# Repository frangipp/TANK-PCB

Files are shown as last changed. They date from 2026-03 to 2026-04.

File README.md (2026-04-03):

Dans le cadre d’un projet étudiant en binôme à l’ESEO Angers.

Développement d’un "TANK" : un petit robot à entraînement différentiel. Il sera commandé par Bluetooth via une application Android.
Pour l’utilisateur, l’objectif sera d’entrer en collision avec le TANK adverse. Chaque collision rapporte des points.

Détails techniques :

* Microcontrôleur STM32G431
* Module Bluetooth HC-05
* Négociation USB Power Delivery (STUSB4531)
* Chargeur et BMS pour batterie Li-ion (power management : BQ24800, équilibrage des cellules : BQ76905)
* Driver moteur LMD18200. Moteurs jusqu’à 55 V (théorique) et 3 A. On utilise ici des Maxon en 12 V.

À titre personnel, ce projet me permet surtout de tester la norme USB Power Delivery ainsi que la charge d’une batterie.

### Restrictions on Automated Processing and AI Usage

The author explicitly prohibits any text and data mining (TDM), scraping, indexing, or use of this project for training, evaluating, or operating artificial intelligence systems, unless prior written permission is obtained.

All rights are reserved in this regard, including under applicable EU directives on text and data mining.

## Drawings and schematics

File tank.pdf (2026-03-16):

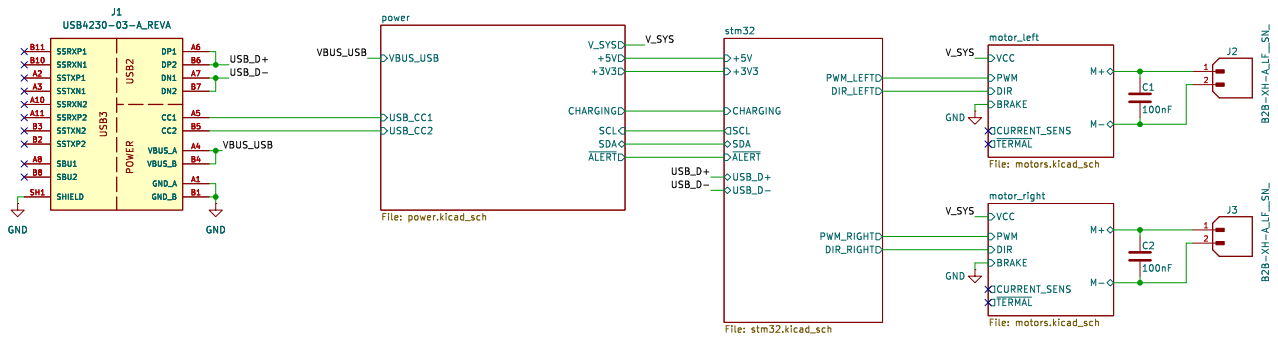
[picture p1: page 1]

motor_right File: motors.kicad_sch SCL SDA

Id: 1/6 Title: File: tank.kicad_sch Sheet: /

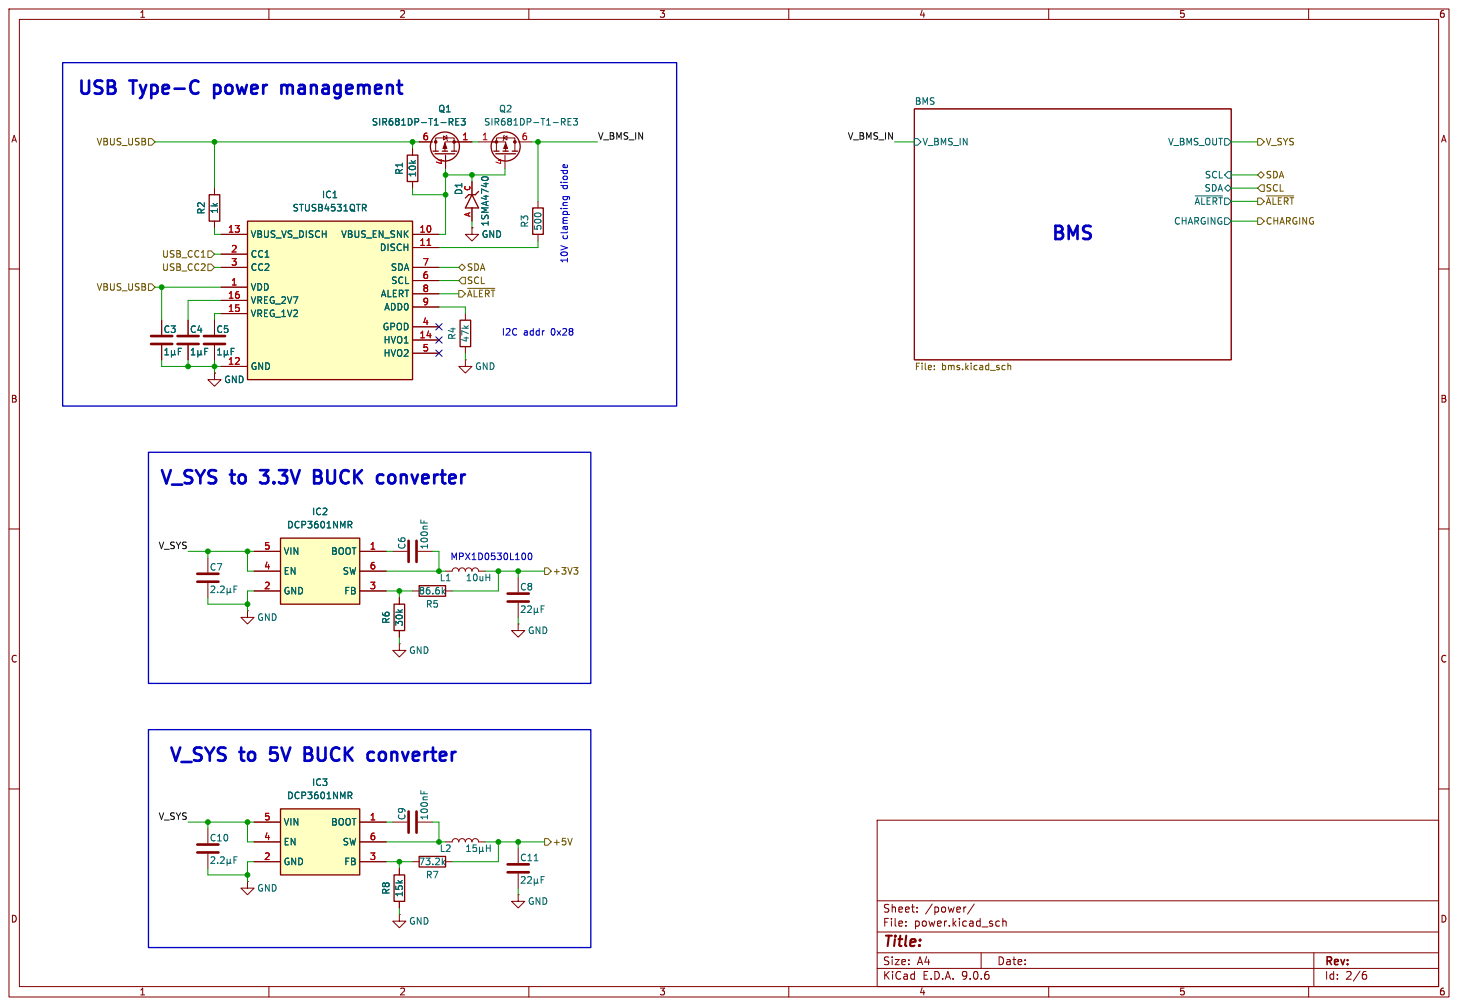
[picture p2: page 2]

Id: 2/6 Title: File: power.kicad_sch Sheet: /power/

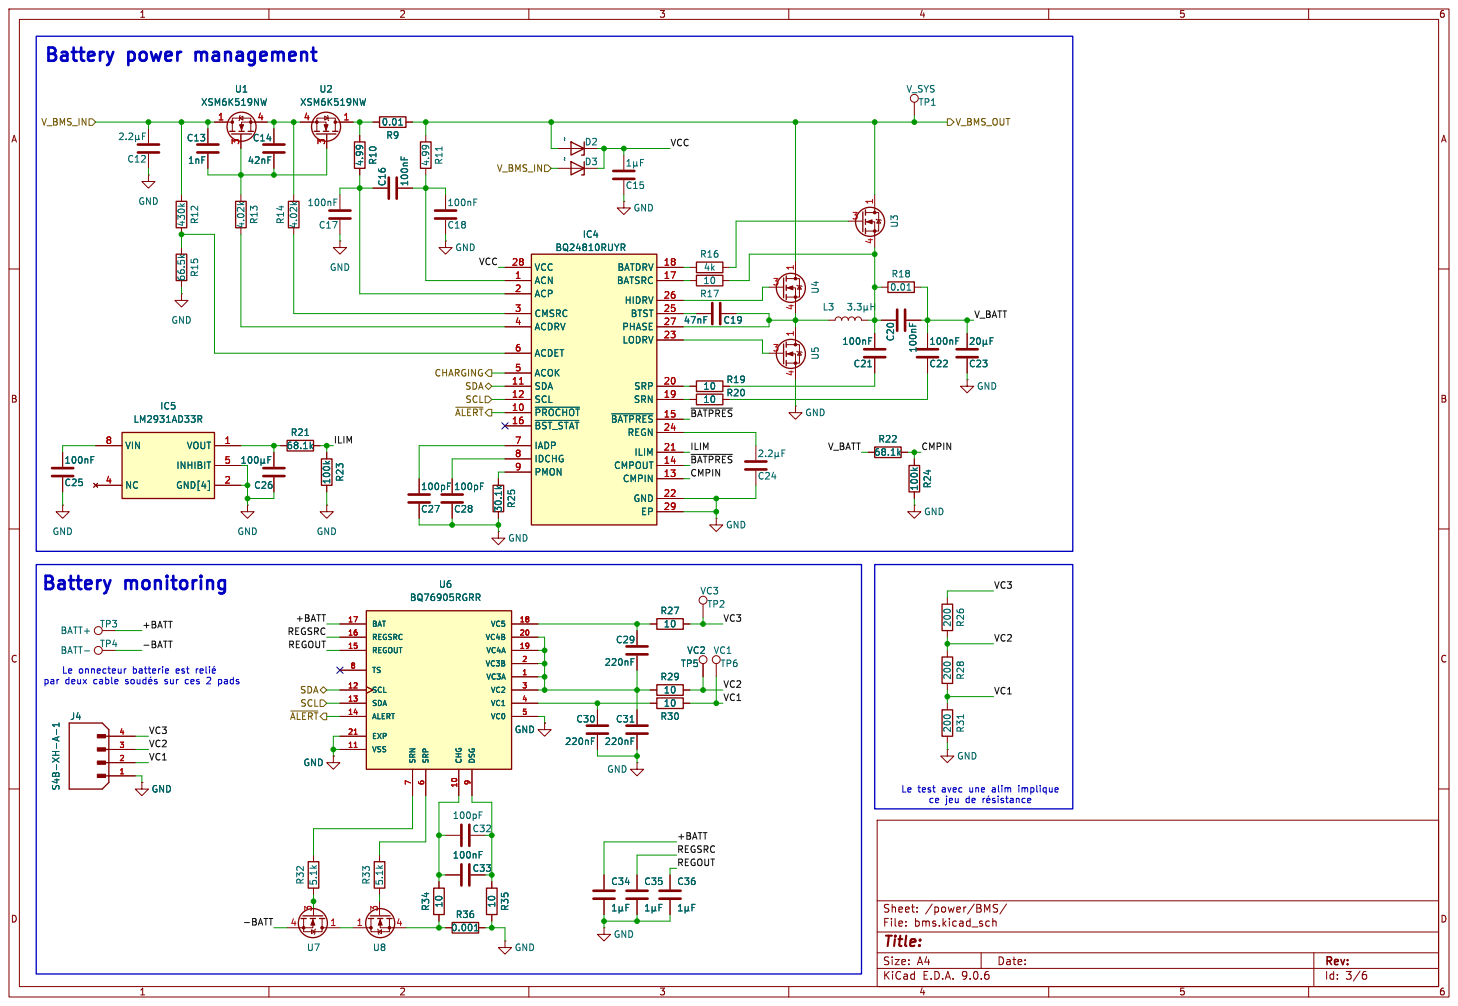
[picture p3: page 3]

Id: 3/6 Title: File: bms.kicad_sch Sheet: /power/BMS/ GND

ce jeu de þÿrésistance

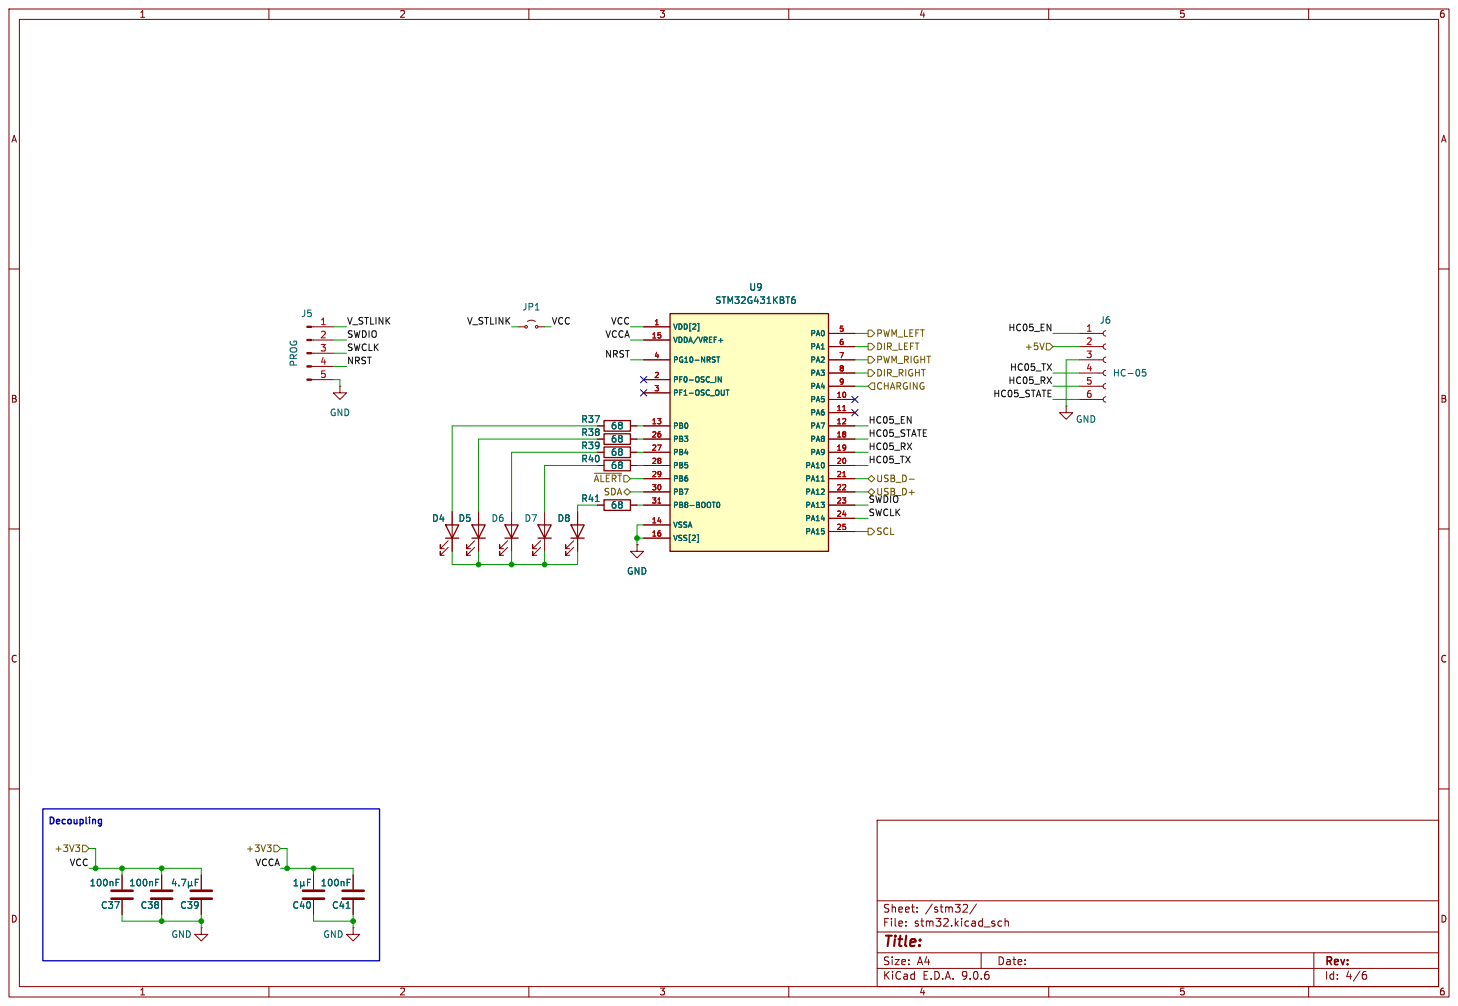
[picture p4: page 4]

þÿ1µFGND
Id: 4/6 Title: File: stm32.kicad_sch Sheet: /stm32/ C40

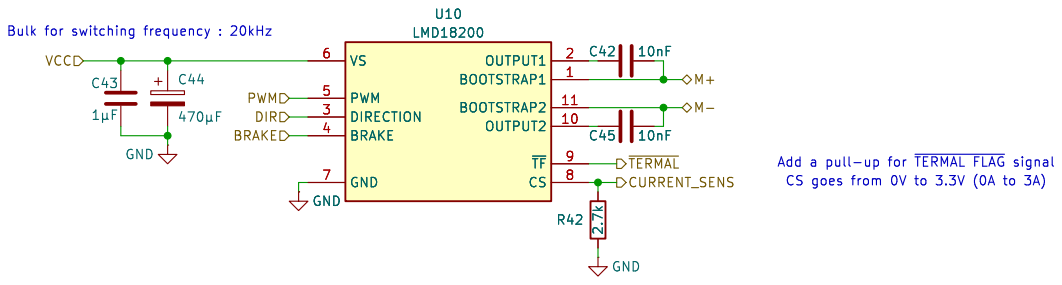
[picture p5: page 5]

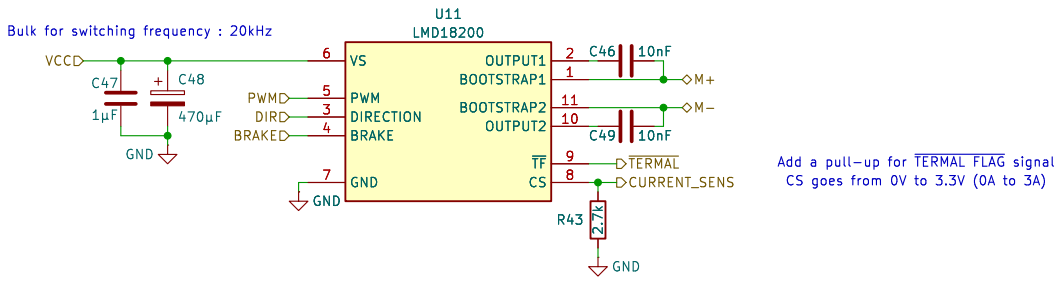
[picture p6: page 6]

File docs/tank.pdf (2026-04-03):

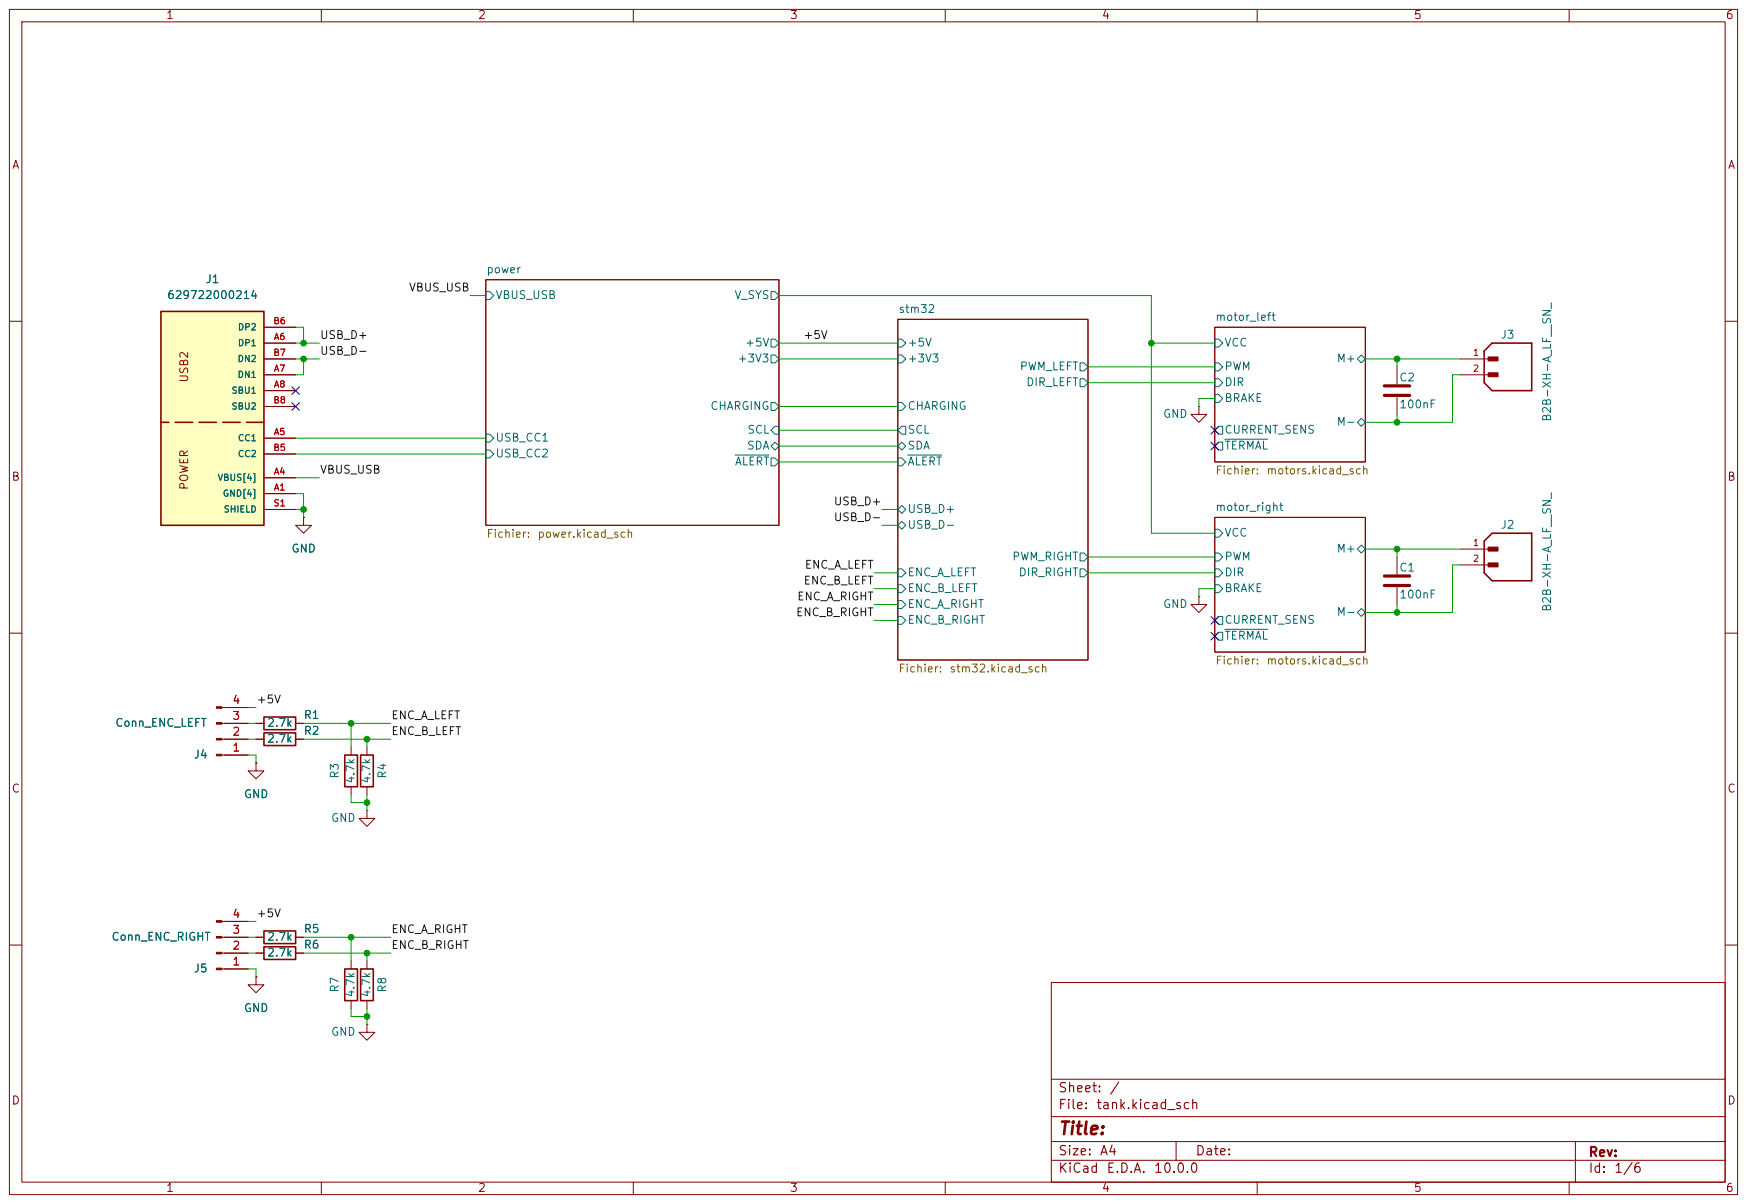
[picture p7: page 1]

TERMAL motor_left Fichier: motors.kicad_sch GND

Size: A4 | Rev:
KiCad E.D.A. 10.0.0 | Id: 1/6

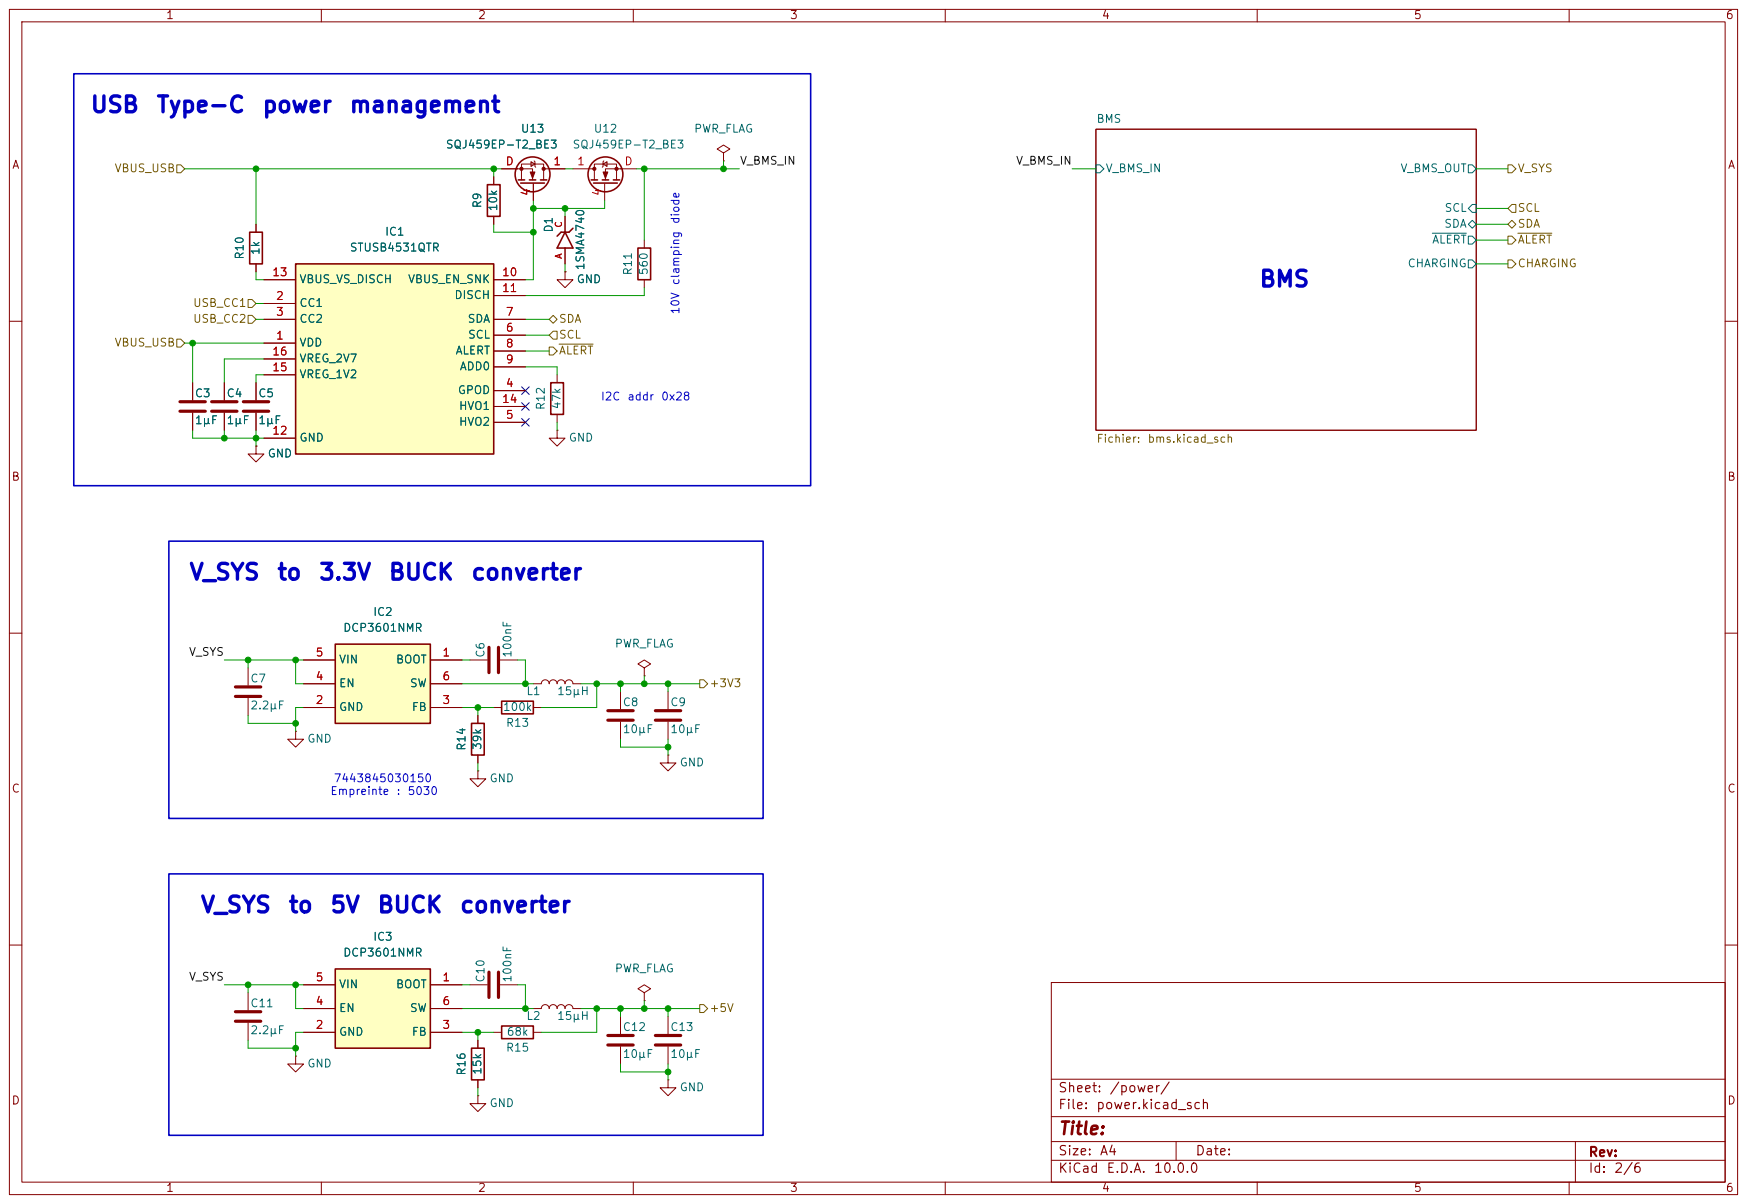
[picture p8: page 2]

USB Type-C power management

Empreinte : 5030 V_SYS to 5V BUCK converter

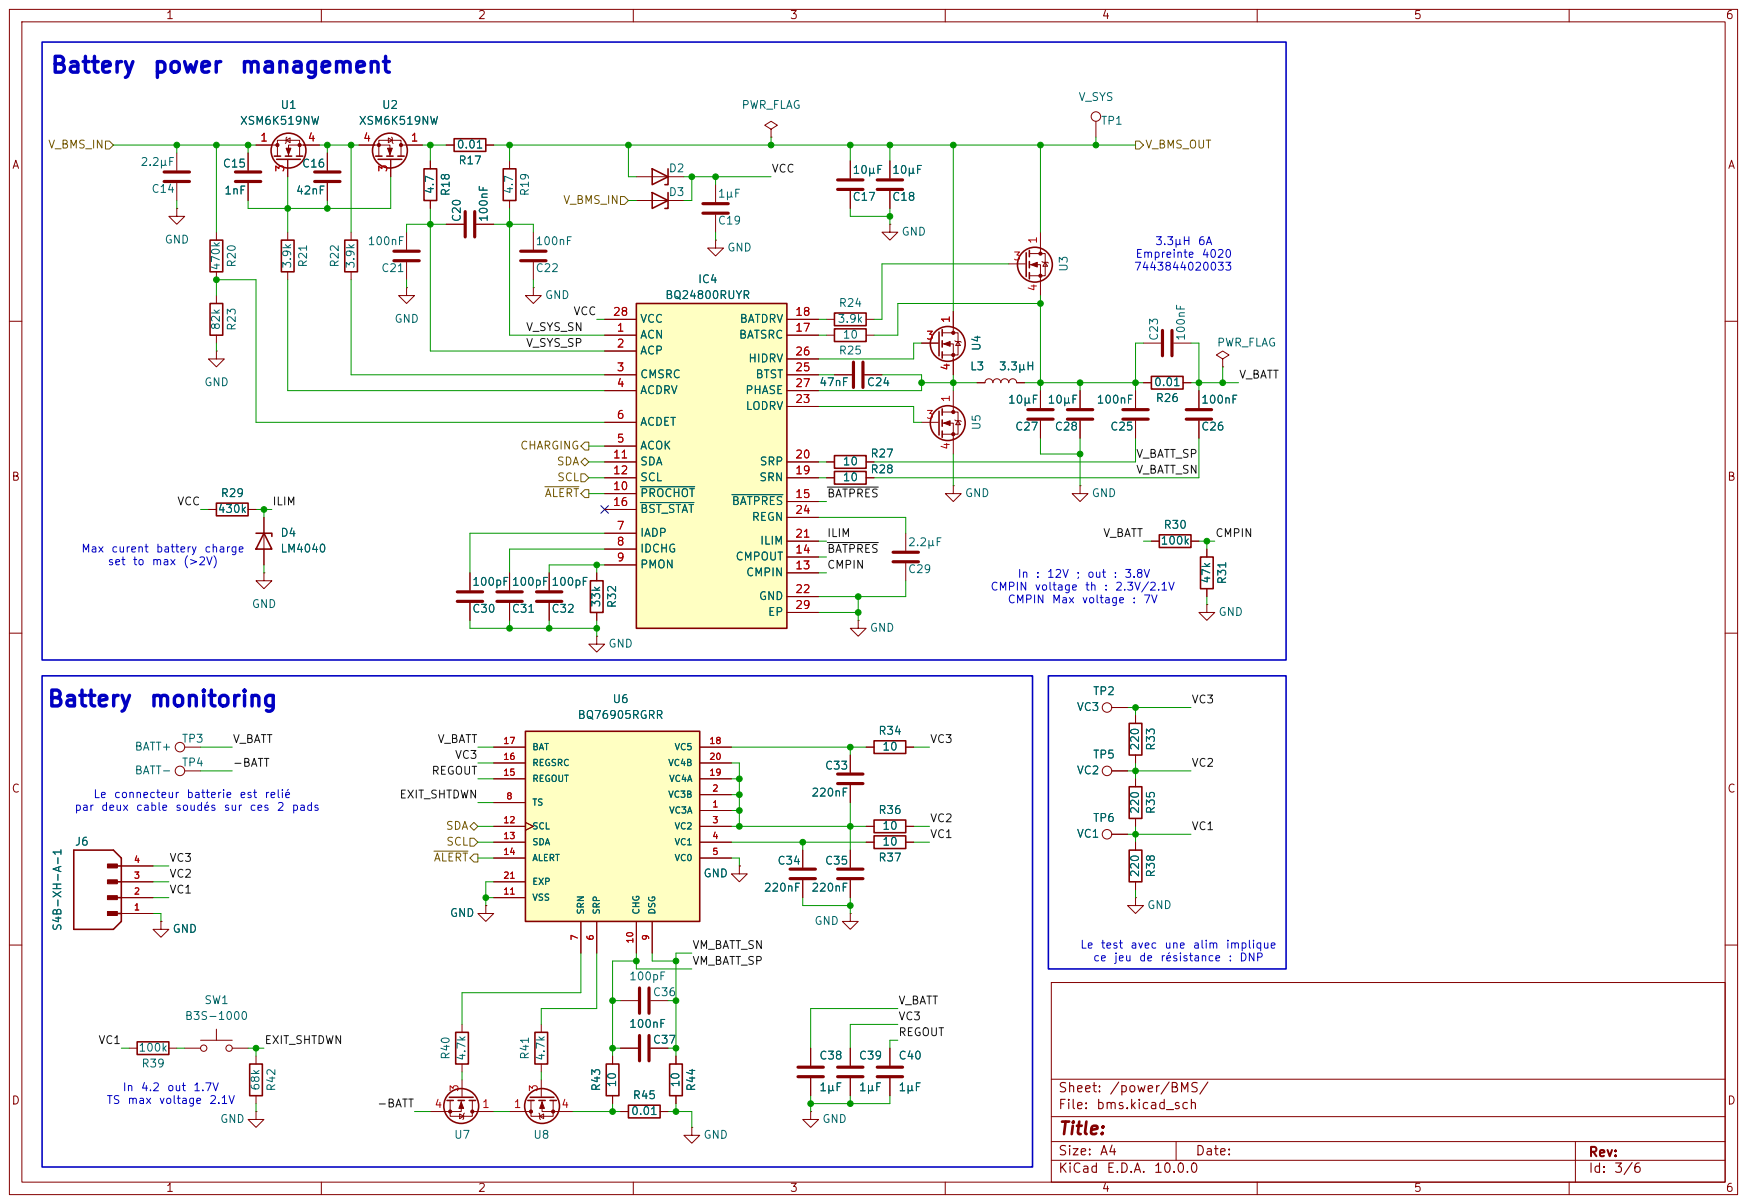
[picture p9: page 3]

ILIM Battery power management

Max curent battery charge

In : 12V ; out : 3.8V CMPIN voltage th : 2.3V/2.1V

Le connecteur batterie est relié par deux cable soudés sur ces 2 pads

Le test avec une alim implique
ce jeu de résistance : DNP

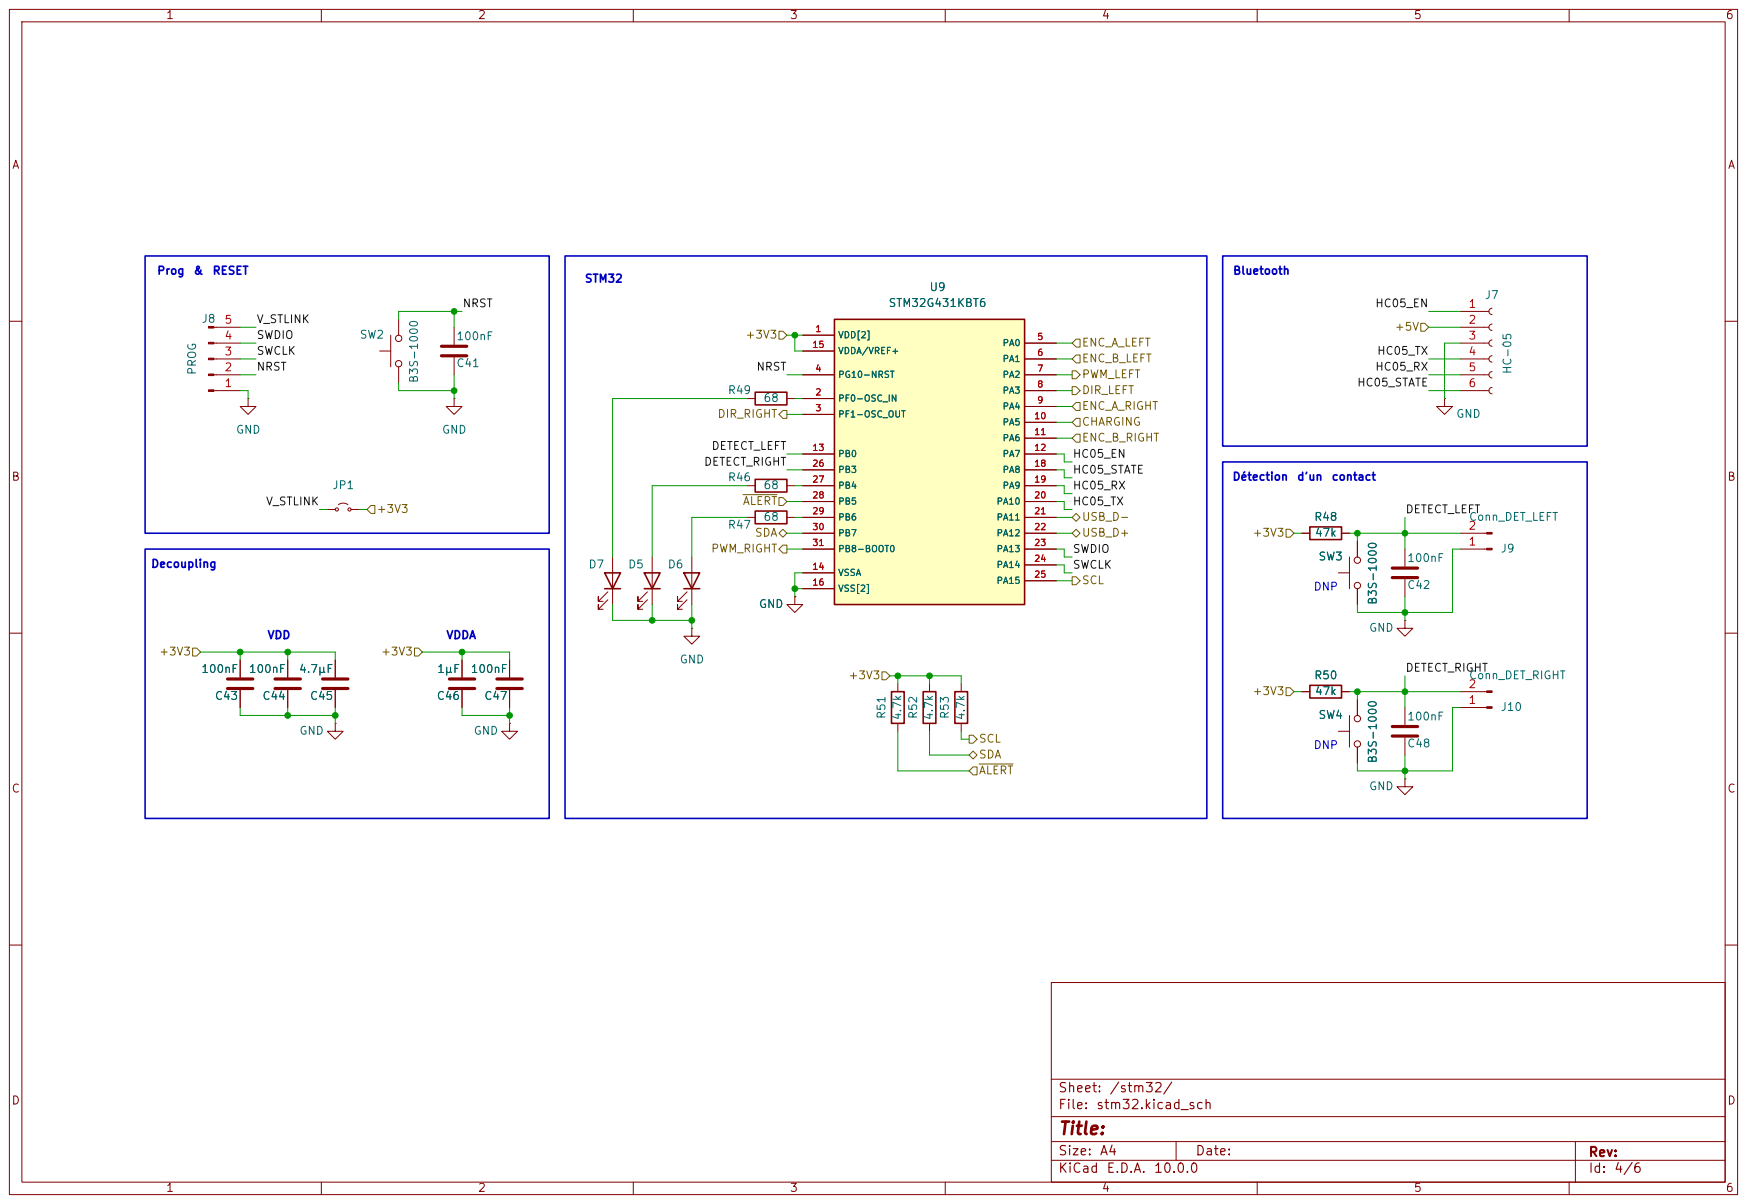
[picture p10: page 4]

Détection d'un contact STM32 Decoupling

AB

C

D

AB

C

### D Date:

## Title:

### File: motors.kicad_sch

### Sheet: /motor_right/

C51

470µF | GND
BOOTSTRAP1 | 1 OUTPUT1 | 2 DIRECTION 3 | BRAKE 4 | PWM 5
VS 6 | GND 7 | CS | 8
TF | 9 OUTPUT2 | 10 BOOTSTRAP2 | 11 U10
LMD18200 | C52 | 10nF C49 | 10nF C50

1µF GND

R54 2.7k GND

CURRENT_SENS BRAKE PWM

VCC

DIR

TERMAL M+

M-

Add a pull-up for TERMAL FLAG signal

Capa 470µF 63V 865080763016 Bulk for switching frequency : 20kHz | CS goes from 0V to 3.3V (0A to 3A) C52 | 10nF C49 | 10nF GND
R54 | 2.7k U10
LMD18200 BOOTSTRAP1 | 1 OUTPUT1 | 2 DIRECTION 3 | BRAKE 4 | PWM 5
VS 6 | GND 7 | CS | 8
TF | 9 OUTPUT2 | 10 BOOTSTRAP2 | 11

AB

C

D

AB

C

### D Date:

## Title:

### File: motors.kicad_sch

### Sheet: /motor_left/

C55

470µF | GND
BOOTSTRAP1 | 1 OUTPUT1 | 2 DIRECTION 3 | BRAKE 4 | PWM 5
VS 6 | GND 7 | CS | 8
TF | 9 OUTPUT2 | 10 BOOTSTRAP2 | 11 U11
LMD18200 | C56 | 10nF C53 | 10nF C54

1µF GND

R55 2.7k GND

CURRENT_SENS BRAKE PWM

VCC

DIR

TERMAL M+

M-

Add a pull-up for TERMAL FLAG signal

Capa 470µF 63V 865080763016 Bulk for switching frequency : 20kHz | CS goes from 0V to 3.3V (0A to 3A) C56 | 10nF C53 | 10nF GND
R55 | 2.7k U11
LMD18200 BOOTSTRAP1 | 1 OUTPUT1 | 2 DIRECTION 3 | BRAKE 4 | PWM 5
VS 6 | GND 7 | CS | 8
TF | 9 OUTPUT2 | 10 BOOTSTRAP2 | 11

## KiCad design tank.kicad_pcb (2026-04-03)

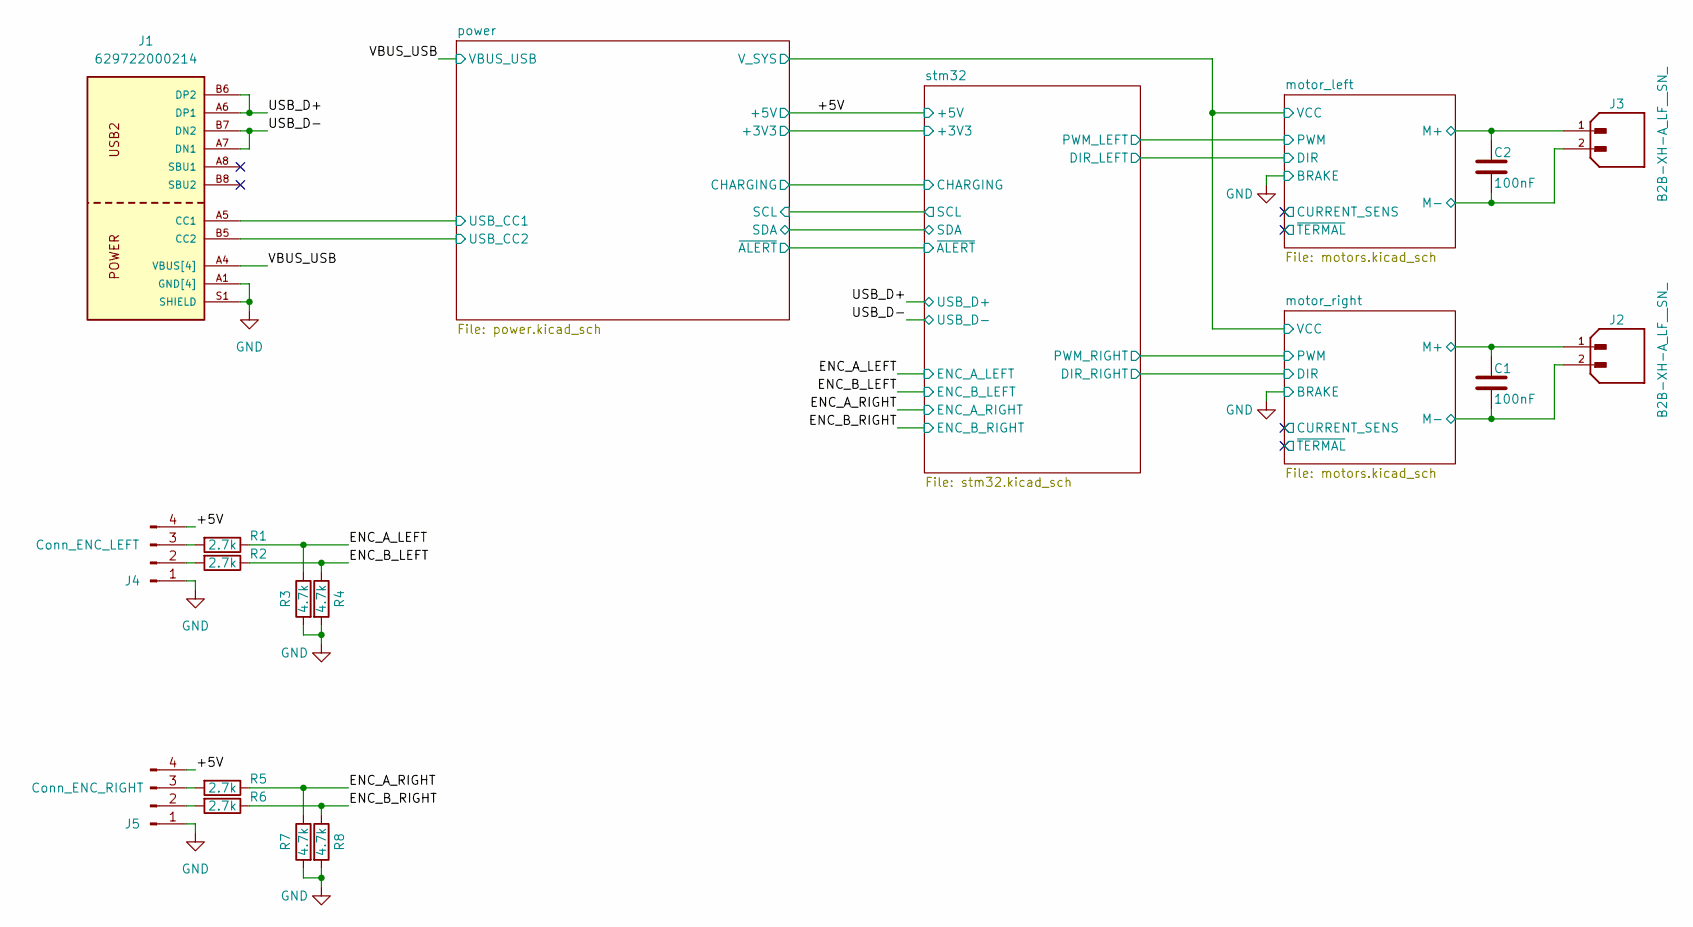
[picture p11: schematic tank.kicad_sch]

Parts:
C1, C2: 100nF; C_0603_1608Metric
J1: 629722000214
J2, J3: B2B-XH-A_LF__SN_; JST_B2B-XH-A_LF__SN_
J4: Conn_ENC_LEFT; PinHeader_1x04_P2.54mm_Vertical
J5: Conn_ENC_RIGHT; PinHeader_1x04_P2.54mm_Vertical
R1, R2, R5, R6: 2.7k; R_0603_1608Metric
R3, R4, R7, R8: 4.7k; R_0603_1608Metric

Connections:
/+5V: J4.4, J5.4; also elsewhere on the board
/ENC_A_LEFT: R1.1, R3.1; also elsewhere on the board
/ENC_A_RIGHT: R5.1, R7.1; also elsewhere on the board
/ENC_B_LEFT: R2.1, R4.1; also elsewhere on the board
/ENC_B_RIGHT: R6.1, R8.1; also elsewhere on the board
/USB_D+: J1.A6 (DP1), J1.B6 (DP2); also elsewhere on the board
/USB_D-: J1.A7 (DN1), J1.B7 (DN2); also elsewhere on the board
/VBUS_USB: J1.A4 (VBUS[4]), J1.A9 (VBUS[4]), J1.B4 (VBUS[4]), J1.B9 (VBUS[4]); also elsewhere on the board
/motor_left/M+: C2.1, J3.1; also elsewhere on the board
/motor_left/M-: C2.2, J3.2; also elsewhere on the board
/motor_right/M+: C1.1, J2.1; also elsewhere on the board
/motor_right/M-: C1.2, J2.2; also elsewhere on the board
/power/USB_CC1: J1.A5 (CC1); also elsewhere on the board
/power/USB_CC2: J1.B5 (CC2); also elsewhere on the board
GND: J1.A1 (GND[4]), J1.A12 (GND[4]), J1.B1 (GND[4]), J1.B12 (GND[4]), J1.S1 (SHIELD), J1.S2, J1.S3, J1.S4, J4.1, J5.1, R3.2, R4.2, R7.2, R8.2; also elsewhere on the board
unnamed: J4.2, R2.2
unnamed: J4.3, R1.2
unnamed: J5.2, R6.2
unnamed: J5.3, R5.2

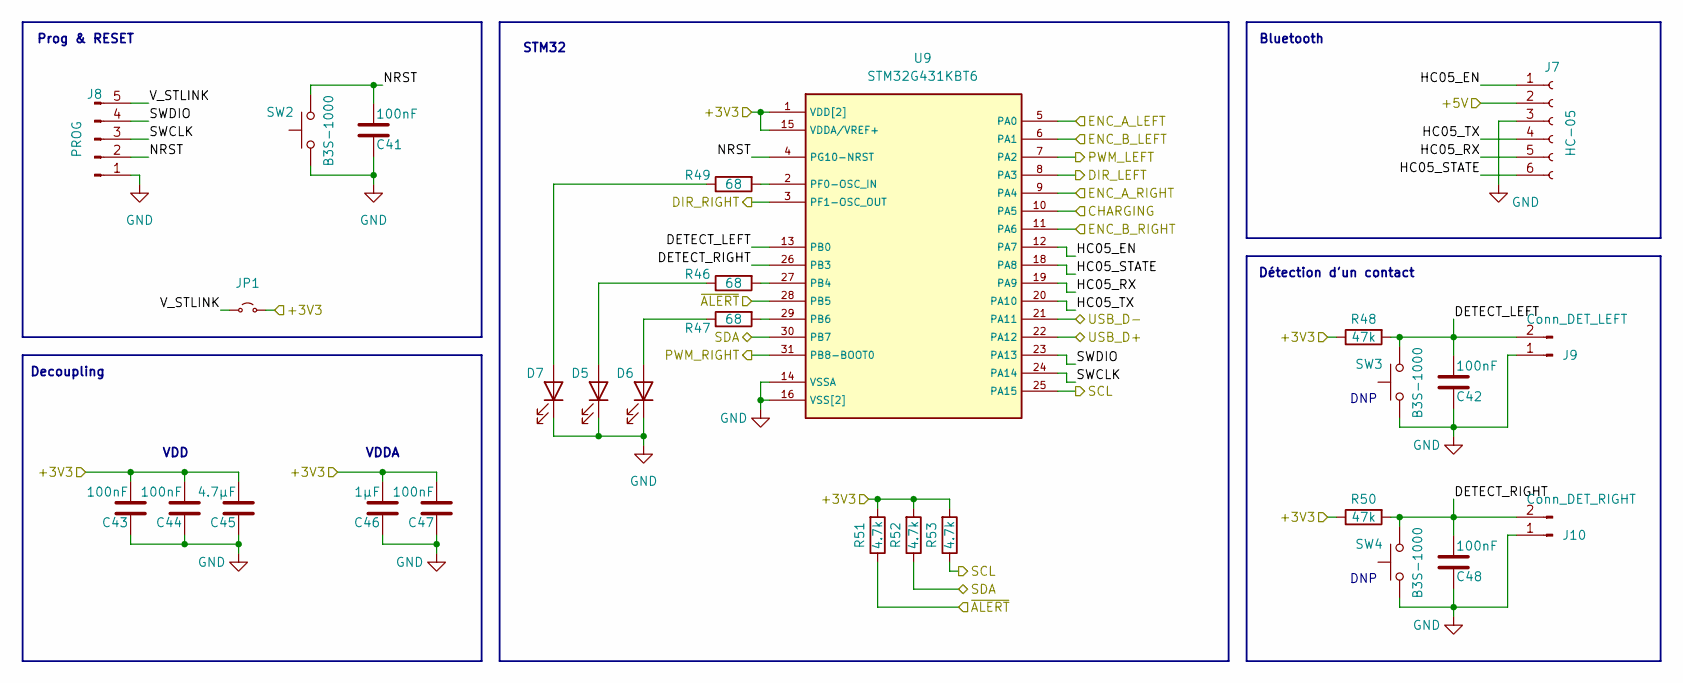
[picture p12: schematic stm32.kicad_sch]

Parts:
C41, C42, C43, C44, C47, C48: 100nF; C_0603_1608Metric
C45: 4.7µF; C_0805_2012Metric
C46: 1µF; C_0603_1608Metric
D5, D6, D7: LED; LED_0603_1608Metric
J7: HC-05; PinSocket_1x06_P2.54mm_Vertical
J8: PROG; PinHeader_1x05_P2.54mm_Vertical
J9: Conn_DET_LEFT; PinHeader_1x02_P2.54mm_Vertical
J10: Conn_DET_RIGHT; PinHeader_1x02_P2.54mm_Vertical
JP1: Jumper_2_Small_Open; PinHeader_1x02_P2.54mm_Vertical
R46, R47, R49: 68; R_0603_1608Metric
R48, R50: 47k; R_0603_1608Metric
R51, R52, R53: 4.7k; R_0603_1608Metric
SW2, SW3, SW4: B3S-1000; SW_SPST_B3S-1000
U9: STM32G431KBT6; QFP80P900X900X160-32N

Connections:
/+5V: J7.2; also elsewhere on the board
/ENC_A_LEFT: U9.5 (PA0); also elsewhere on the board
/ENC_A_RIGHT: U9.9 (PA4); also elsewhere on the board
/ENC_B_LEFT: U9.6 (PA1); also elsewhere on the board
/ENC_B_RIGHT: U9.11 (PA6); also elsewhere on the board
/USB_D+: U9.22 (PA12); also elsewhere on the board
/USB_D-: U9.21 (PA11); also elsewhere on the board
/motor_left/DIR: U9.8 (PA3); also elsewhere on the board
/motor_left/PWM: U9.7 (PA2); also elsewhere on the board
/motor_right/DIR: U9.3 (PF1-OSC_OUT); also elsewhere on the board
/motor_right/PWM: U9.31 (PB8-BOOT0); also elsewhere on the board
/power/CHARGING: U9.10 (PA5); also elsewhere on the board
/power/SCL: R53.1, U9.25 (PA15); also elsewhere on the board
/power/SDA: R52.1, U9.30 (PB7); also elsewhere on the board
/power/~ALERT: R51.1, U9.28 (PB5); also elsewhere on the board
/stm32/DETECT_LEFT: C42.2, J9.2, R48.2, SW3.2, U9.13 (PB0)
/stm32/DETECT_RIGHT: C48.2, J10.2, R50.2, SW4.2, U9.26 (PB3)
/stm32/HC05_EN: J7.1, U9.12 (PA7)
/stm32/HC05_RX: J7.5, U9.19 (PA9)
/stm32/HC05_STATE: J7.6, U9.18 (PA8)
/stm32/HC05_TX: J7.4, U9.20 (PA10)
/stm32/NRST: C41.2, J8.2, SW2.2, U9.4 (PG10-NRST)
/stm32/SWCLK: J8.3, U9.24 (PA14)
/stm32/SWDIO: J8.4, U9.23 (PA13)
/stm32/V_STLINK: J8.5, JP1.1 (A)
GND: C41.1, C42.1, C43.1, C44.1, C45.1, C46.1, C47.1, C48.1, D5.1 (K), D6.1 (K), D7.1 (K), J7.3, J8.1, J9.1, J10.1, SW2.1, SW3.1, SW4.1, U9.14 (VSSA), U9.16 (VSS[2]), U9.32 (VSS); also elsewhere on the board
unnamed: D5.2 (A), R46.1
unnamed: D6.2 (A), R47.1
unnamed: D7.2 (A), R49.1
unnamed: R46.2, U9.27 (PB4)
unnamed: R47.2, U9.29 (PB6)
unnamed: R49.2, U9.2 (PF0-OSC_IN)
VDD: C43.2, C44.2, C45.2, C46.2, C47.2, JP1.2 (B), R48.1, R50.1, R51.2, R52.2, R53.2, U9.1 (VDD[2]), U9.15 (VDDA/VREF+), U9.17 (VDD); also elsewhere on the board

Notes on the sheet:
VDDA
Détection d'un contact
Bluetooth
DNP
VDD
Decoupling
Prog & RESET
STM32

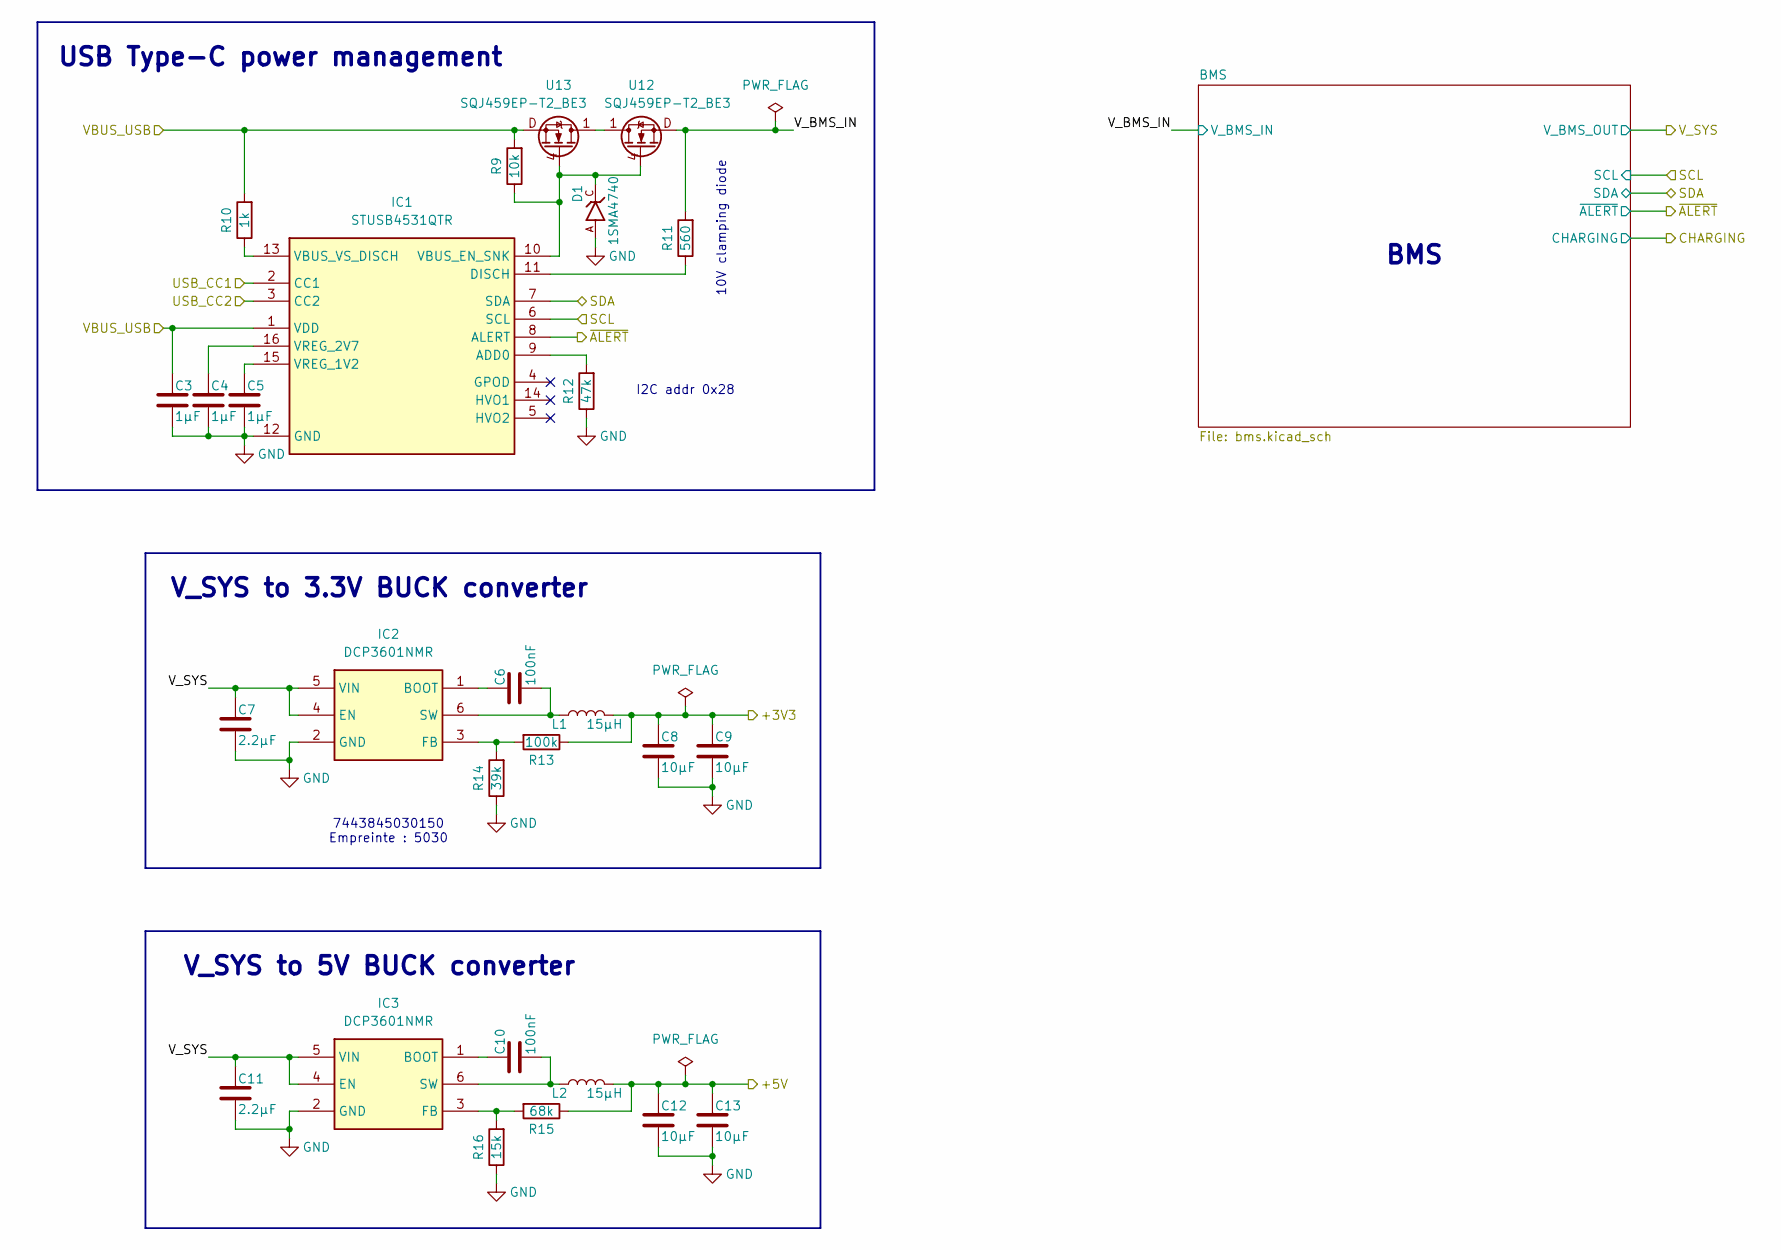
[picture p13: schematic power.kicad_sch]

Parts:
C3, C4, C5: 1µF; C_0603_1608Metric
C6, C10: 100nF; C_0603_1608Metric
C7, C11: 2.2µF; C_0603_1608Metric
C8, C9, C12, C13: 10µF; C_0805_2012Metric
D1: 1SMA4740; DIOM4325X250N
IC1: STUSB4531QTR; QFN50P300X300X65-16N-D
IC2, IC3: DCP3601NMR; SOT95P280X125-6N; Mouser Part Number 511-DCP3601NMR
L1, L2: 15µH; L_Wuerth_MAPI-5030
R9: 10k; R_0603_1608Metric
R10: 1k; R_0603_1608Metric
R11: 560; R_0603_1608Metric
R12: 47k; R_0603_1608Metric
R13: 100k; R_0603_1608Metric
R14: 39k; R_0603_1608Metric
R15: 68k; R_0603_1608Metric
R16: 15k; R_0603_1608Metric
U12, U13: SQJ459EP-T2_BE3; SIJA54DPT1GE3

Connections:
/+5V: C12.1, C13.1, L2.2, R15.1; also elsewhere on the board
/VBUS_USB: C3.1, IC1.1 (VDD), R9.2, R10.2, U13.D; also elsewhere on the board
/power/SCL: IC1.6 (SCL); also elsewhere on the board
/power/SDA: IC1.7 (SDA); also elsewhere on the board
/power/USB_CC1: IC1.2 (CC1); also elsewhere on the board
/power/USB_CC2: IC1.3 (CC2); also elsewhere on the board
/power/V_BMS_IN: R11.2, U12.D; also elsewhere on the board
/power/V_SYS: C7.1, C11.1, IC2.4 (EN), IC2.5 (VIN), IC3.4 (EN), IC3.5 (VIN); also elsewhere on the board
/power/~ALERT: IC1.8 (ALERT); also elsewhere on the board
GND: C3.2, C4.2, C5.2, C7.2, C8.2, C9.2, C11.2, C12.2, C13.2, D1.A, IC1.12 (GND), IC2.2 (GND), IC3.2 (GND), R12.1, R14.1, R16.1; also elsewhere on the board
unnamed: IC1.9 (ADD0), R12.2
unnamed: IC1.11 (DISCH), R11.1
unnamed: D1.C, IC1.10 (VBUS_EN_SNK), R9.1, U12.4, U13.4
unnamed: IC1.13 (VBUS_VS_DISCH), R10.1
unnamed: C5.1, IC1.15 (VREG_1V2)
unnamed: C4.1, IC1.16 (VREG_2V7)
unnamed: C6.1, IC2.1 (BOOT)
unnamed: IC2.3 (FB), R13.2, R14.2
unnamed: C6.2, IC2.6 (SW), L1.1
unnamed: C10.1, IC3.1 (BOOT)
unnamed: IC3.3 (FB), R15.2, R16.2
unnamed: C10.2, IC3.6 (SW), L2.1
unnamed: U12.1, U12.2, U12.3, U13.1, U13.2, U13.3
VDD: C8.1, C9.1, L1.2, R13.1; also elsewhere on the board

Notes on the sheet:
USB Type-C power management
BMS
V_SYS to 3.3V BUCK converter
I2C addr 0x28
V_SYS to 5V BUCK converter
10V clamping diode
7443845030150 Empreinte : 5030

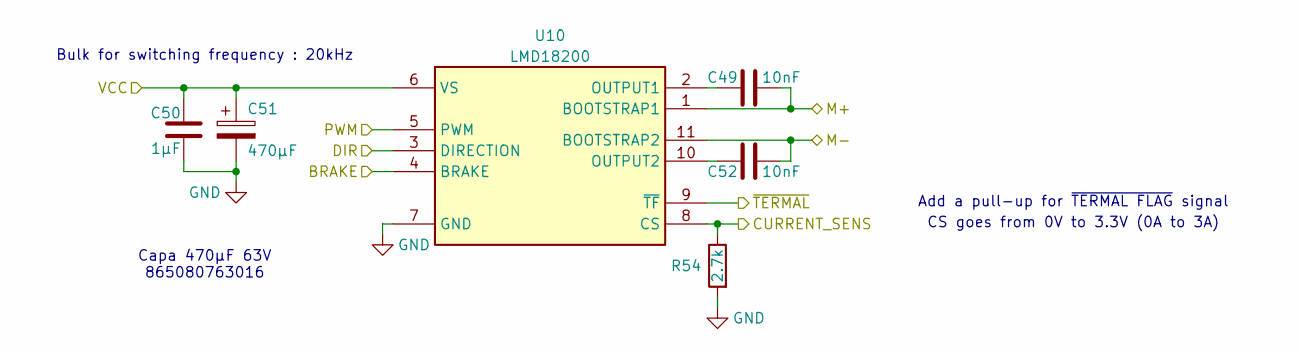
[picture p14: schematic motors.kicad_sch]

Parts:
C49, C52: 10nF; C_0603_1608Metric
C50: 1µF; C_0603_1608Metric
C51: 470µF; CP_Elec_16x17.5
R54: 2.7k; R_0603_1608Metric
U10: LMD18200

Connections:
/motor_right/CURRENT_SENS: R54.1, U10.8 (CS)
/motor_right/DIR: U10.3 (DIRECTION); also elsewhere on the board
/motor_right/M+: C49.2, U10.1 (BOOTSTRAP1); also elsewhere on the board
/motor_right/M-: C52.2, U10.11 (BOOTSTRAP2); also elsewhere on the board
/motor_right/PWM: U10.5 (PWM); also elsewhere on the board
/motor_right/~TERMAL: U10.9 (~TF)
/power/V_SYS: C50.1, C51.1, U10.6 (VS); also elsewhere on the board
GND: C50.2, C51.2, R54.2, U10.4 (BRAKE), U10.7 (GND); also elsewhere on the board
unnamed: C49.1, U10.2 (OUTPUT1)
unnamed: C52.1, U10.10 (OUTPUT2)

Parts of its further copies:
C53, C56: 10nF; C_0603_1608Metric
C54: 1µF; C_0603_1608Metric
C55: 470µF; CP_Elec_16x17.5
R55: 2.7k; R_0603_1608Metric
U11: LMD18200

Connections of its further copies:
/motor_left/CURRENT_SENS: R55.1, U11.8 (CS)
/motor_left/DIR: U11.3 (DIRECTION); also elsewhere on the board
/motor_left/M+: C53.2, U11.1 (BOOTSTRAP1); also elsewhere on the board
/motor_left/M-: C56.2, U11.11 (BOOTSTRAP2); also elsewhere on the board
/motor_left/PWM: U11.5 (PWM); also elsewhere on the board
/motor_left/~TERMAL: U11.9 (~TF)
/power/V_SYS: C54.1, C55.1, U11.6 (VS); also elsewhere on the board
GND: C54.2, C55.2, R55.2, U11.4 (BRAKE), U11.7 (GND); also elsewhere on the board
unnamed: C53.1, U11.2 (OUTPUT1)
unnamed: C56.1, U11.10 (OUTPUT2)

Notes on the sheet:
Add a pull-up for ~{TERMAL FLAG} signal
Bulk for switching frequency : 20kHz
Capa 470µF 63V 865080763016
CS goes from 0V to 3.3V (0A to 3A)

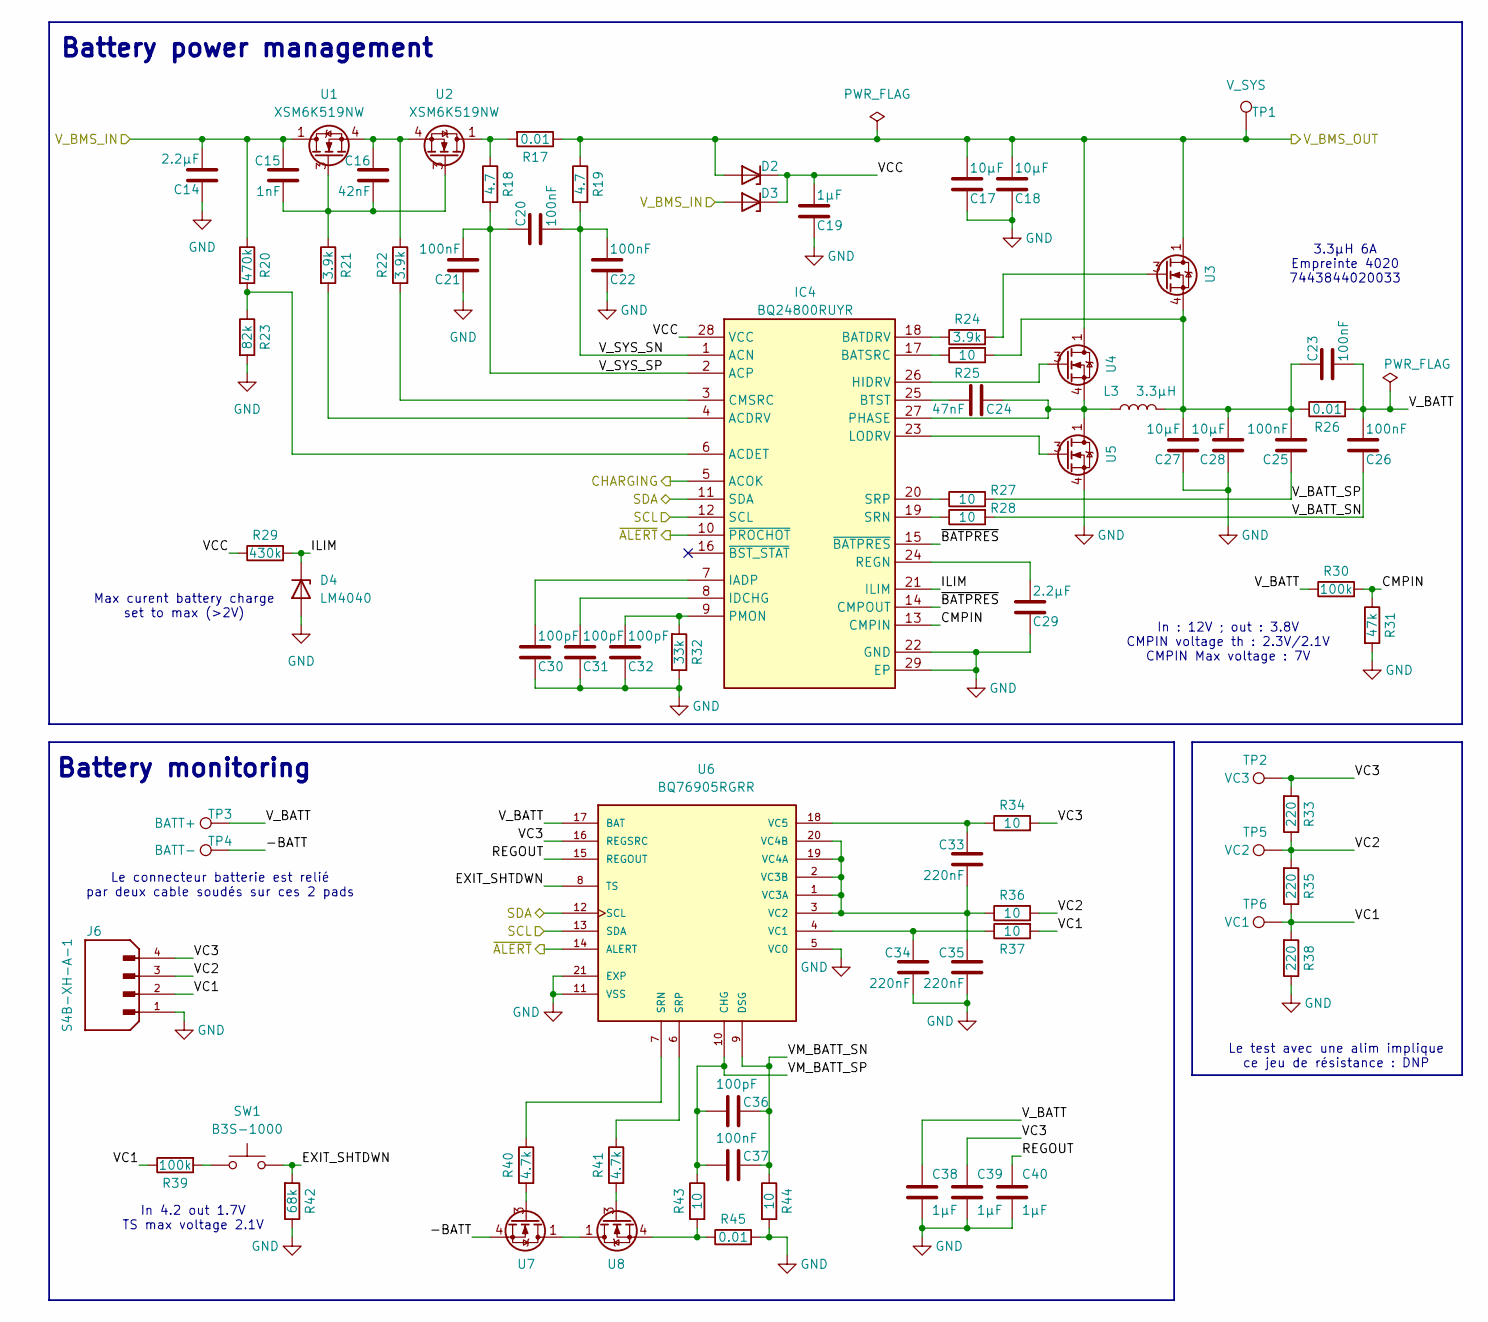
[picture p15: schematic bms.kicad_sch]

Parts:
C14, C29: 2.2µF; C_0603_1608Metric
C15: 1nF; C_0603_1608Metric
C16: 42nF; C_0603_1608Metric
C17, C18, C27, C28: 10µF; C_0805_2012Metric
C19, C38, C39, C40: 1µF; C_0603_1608Metric
C20, C21, C22, C23, C25, C26, C37: 100nF; C_0603_1608Metric
C24: 47nF; C_0603_1608Metric
C30, C31, C32, C36: 100pF; C_0603_1608Metric
C33, C34, C35: 220nF; C_0603_1608Metric
D2, D3: DIO_MM3Z3V0T1G
D4: LM4040; SOT95P237X112-3N
IC4: BQ24800RUYR; QFN40P400X400X80-29N-D; Manufacturer_Part_Number BQ24810RUYR
J6: S4B-XH-A-1; JST_S4B-XH-A-1
L3: 3.3µH; L_Wuerth_MAPI-4020
R17, R26, R45: 0.01; RESC6331X88N
R18, R19: 4.7; R_0603_1608Metric
R20: 470k; R_0603_1608Metric
R21, R22, R24: 3.9k; R_0603_1608Metric
R23: 82k; R_0603_1608Metric
R25, R27, R28, R34, R36, R37, R43, R44: 10; R_0603_1608Metric
R29: 430k; R_0603_1608Metric
R30, R39: 100k; R_0603_1608Metric
R31: 47k; R_0603_1608Metric
R32: 33k; R_0603_1608Metric
R33, R35, R38: 220; R_0805_2012Metric
R40, R41: 4.7k; R_0603_1608Metric
R42: 68k; R_0603_1608Metric
SW1: B3S-1000; SW_SPST_B3S-1000
TP1: V_SYS; TestPoint_Pad_D1.0mm
TP2: VC3; TestPoint_Pad_D1.0mm
TP3: BATT+; TestPoint_THTPad_D4.0mm_Drill2.0mm
TP4: BATT-; TestPoint_THTPad_D4.0mm_Drill2.0mm
TP5: VC2; TestPoint_Pad_D1.0mm
TP6: VC1; TestPoint_Pad_D1.0mm
U1, U2, U3, U4, U5, U7, U8: XSM6K519NW; DFN2020MD-6_SOT1220_NEX
U6: BQ76905RGRR; IC_BQ76905RGRR

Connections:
/power/BMS/-BATT: TP4.1 (1_1), U7.4, U7.8
/power/BMS/CMPIN: IC4.13 (CMPIN), R30.2, R31.1
/power/BMS/EXIT_SHTDWN: R42.2, SW1.2, U6.8 (TS)
/power/BMS/ILIM: D4.1 (K), IC4.21 (ILIM), R29.2
/power/BMS/REGOUT: C40.2, U6.15 (REGOUT)
/power/BMS/VC1: J6.2, R35.1, R37.2, R38.2, R39.1, TP6.1 (1_1)
/power/BMS/VC2: J6.3, R33.1, R35.2, R36.2, TP5.1 (1_1)
/power/BMS/VC3: C39.2, J6.4, R33.2, R34.2, TP2.1 (1_1), U6.16 (REGSRC)
/power/BMS/VCC: C19.2, D2.1 (K), D3.1 (K), IC4.28 (VCC), R29.1
/power/BMS/VM_BATT_SN: C36.1, C37.1, R44.1, U6.9 (DSG)
/power/BMS/VM_BATT_SP: C36.2, C37.2, R43.1, U6.10 (CHG)
/power/BMS/V_BATT: C23.2, C26.2, C38.2, R26.2, R30.1, TP3.1 (1_1), U6.17 (BAT)
/power/BMS/V_BATT_SN: C26.1, R28.2
/power/BMS/V_BATT_SP: C25.1, R27.2
/power/BMS/V_SYS_SN: C20.2, C22.2, IC4.1 (ACN), R19.2
/power/BMS/V_SYS_SP: C20.1, C21.2, IC4.2 (ACP), R18.2
/power/BMS/~BATPRES: IC4.14 (CMPOUT), IC4.15 (~BATPRES)
/power/CHARGING: IC4.5 (ACOK); also elsewhere on the board
/power/SCL: IC4.12 (SCL), U6.13 (SDA); also elsewhere on the board
/power/SDA: IC4.11 (SDA), U6.12 (SCL); also elsewhere on the board
/power/V_BMS_IN: C14.2, C15.1, D3.2 (A), R20.1, U1.1, U1.2, U1.5, U1.6, U1.7; also elsewhere on the board
/power/V_SYS: C17.2, C18.2, D2.2 (A), R17.1, R19.1, TP1.1 (1_1), U3.1, U3.2, U3.5, U3.6, U3.7, U4.1, U4.2, U4.5, U4.6, U4.7; also elsewhere on the board
/power/~ALERT: IC4.10 (~PROCHOT), U6.14 (ALERT); also elsewhere on the board
GND: C14.1, C17.1, C18.1, C19.1, C21.1, C22.1, C27.1, C28.1, C29.1, C30.1, C31.1, C32.1, C34.2, C35.2, C38.1, C39.1, C40.1, D4.2 (A), D4.3 (*), IC4.22 (GND), IC4.29 (EP), J6.1, R23.2, R31.2, R32.1, R38.1, R42.1, R44.2, R45.2, U5.4, U5.8, U6.5 (VC0), U6.11 (VSS), U6.21 (EXP); also elsewhere on the board
unnamed: C15.2, C16.2, R21.1, U1.3, U2.3
unnamed: C16.1, R22.1, U1.4, U1.8, U2.4, U2.8
unnamed: C23.1, C25.2, C27.2, C28.2, L3.2, R25.2, R26.1, U3.4, U3.8
unnamed: IC4.6 (ACDET), R20.2, R23.1
unnamed: IC4.4 (ACDRV), R21.2
unnamed: IC4.18 (BATDRV), R24.1
unnamed: IC4.17 (BATSRC), R25.1
unnamed: C24.2, IC4.25 (BTST)
unnamed: IC4.3 (CMSRC), R22.2
unnamed: IC4.26 (HIDRV), U4.3
unnamed: C30.2, IC4.7 (IADP)
unnamed: C31.2, IC4.8 (IDCHG)
unnamed: IC4.23 (LODRV), U5.3
unnamed: C24.1, IC4.27 (PHASE), L3.1, U4.4, U4.8, U5.1, U5.2, U5.5, U5.6, U5.7
unnamed: C32.2, IC4.9 (PMON), R32.2
unnamed: C29.2, IC4.24 (REGN)
unnamed: IC4.19 (SRN), R28.1
unnamed: IC4.20 (SRP), R27.1
unnamed: R17.2, R18.1, U2.1, U2.2, U2.5, U2.6, U2.7
unnamed: R24.2, U3.3
unnamed: R39.2, SW1.1
unnamed: R40.2, U7.3
unnamed: R41.2, U8.3
unnamed: R43.2, R45.1, U8.4, U8.8
unnamed: R40.1, U6.7 (SRN)
unnamed: R41.1, U6.6 (SRP)
unnamed: C34.1, R37.1, U6.4 (VC1)
unnamed: C33.2, C35.1, R36.1, U6.1 (VC3A), U6.2 (VC3B), U6.3 (VC2), U6.19 (VC4A), U6.20 (VC4B)
unnamed: C33.1, R34.1, U6.18 (VC5)
unnamed: U7.1, U7.2, U7.5, U7.6, U7.7, U8.1, U8.2, U8.5, U8.6, U8.7

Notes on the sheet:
Le connecteur batterie est relié par deux cable soudés sur ces 2 pads
In : 12V ; out : 3.8V CMPIN voltage th : 2.3V/2.1V CMPIN Max voltage : 7V
Battery power management
Max curent battery charge set to max (>2V)
3.3µH 6A Empreinte 4020 7443844020033
In 4.2 out 1.7V TS max voltage 2.1V
Battery monitoring
Le test avec une alim implique ce jeu de résistance : DNP

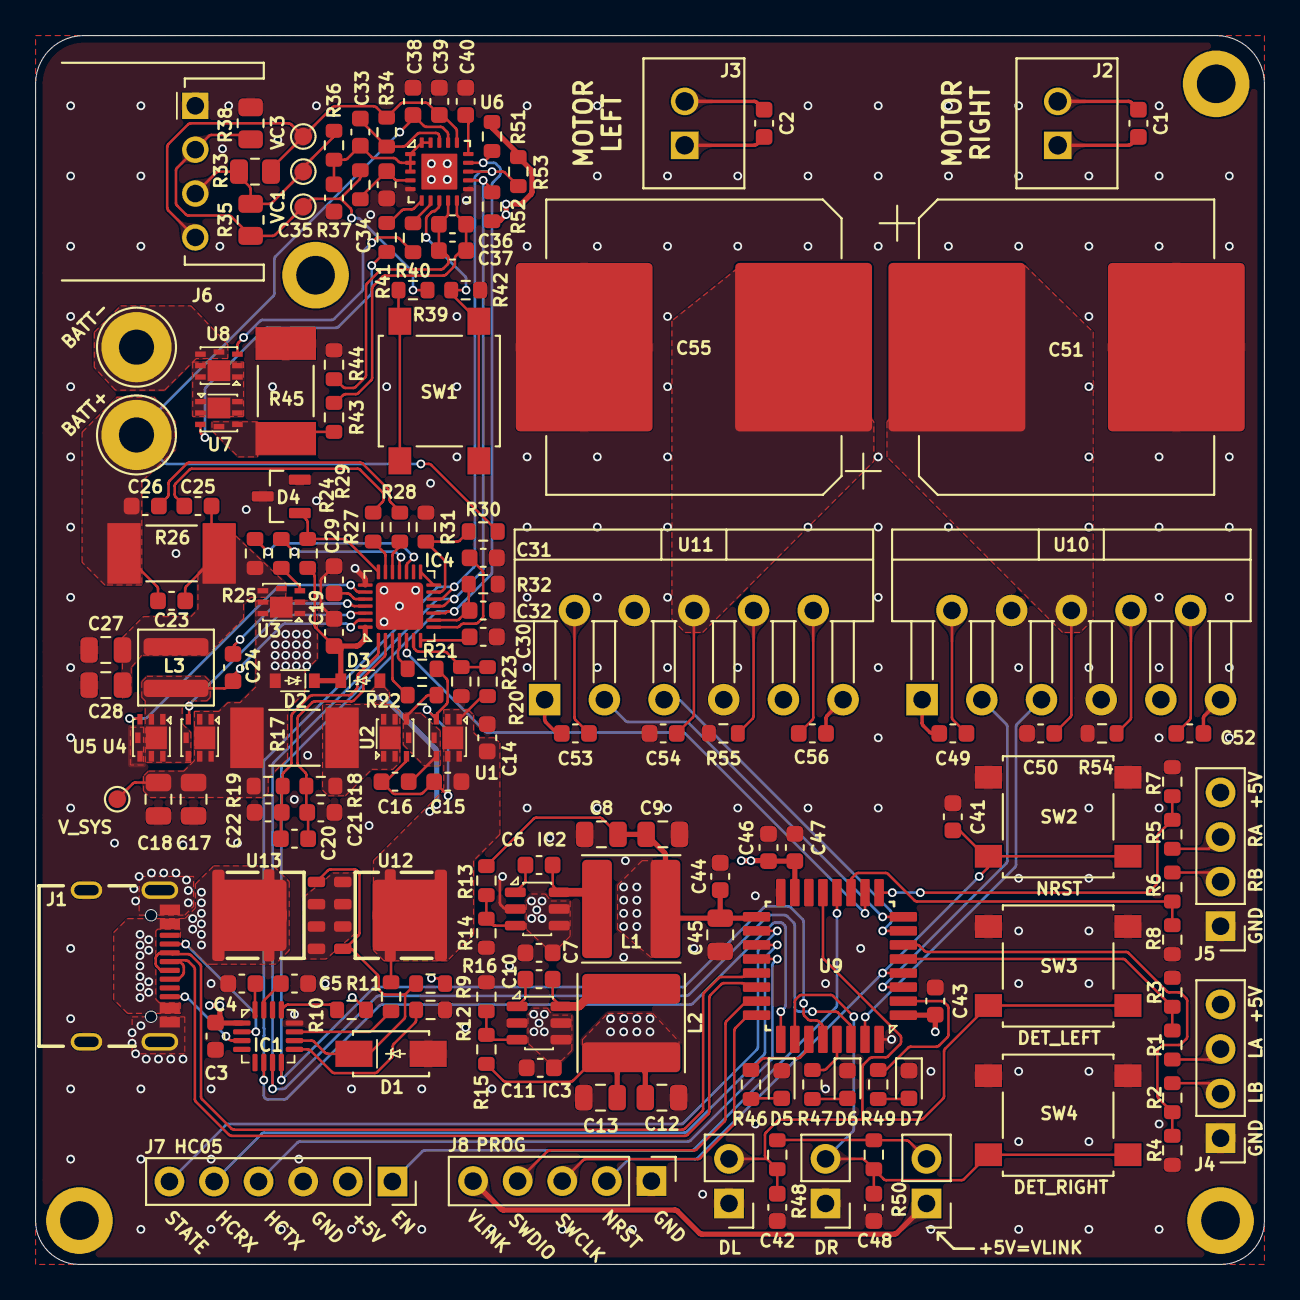
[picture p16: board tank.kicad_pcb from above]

Board: 4 copper layers, 70.0 x 70.0 mm, 159 parts (0 on the bottom side), 112 nets.

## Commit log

2026-03-11 Ajouts de 3 feuilles de travail (motors/stm32/power). Ajout de la négociation USB-PD. Ajout d'un régulateur BUCK 3,3V.
    [bms.kicad_sch, motors.kicad_sch, power.kicad_sch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]
2026-03-12 Ajout du BMS
    [bms.kicad_sch, power.kicad_sch, tank.kicad_sch]
2026-03-14 Update BMS
    [bms.kicad_sch, power.kicad_sch, tank.kicad_sch]
2026-03-14 Ajout des deux moteurs
    [motors.kicad_sch, stm32.kicad_sch, tank.kicad_sch]
2026-03-16 Version 0. Schémas finalisés. Mise à jour des résistances en série E12. Réduction de la BOM.
    [bms.kicad_sch, motors.kicad_sch, power.kicad_sch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]
2026-03-25 Minor Schematics update
    [bms.kicad_sch, motors.kicad_sch, power.kicad_sch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]
2026-03-31 Modification mineur du schéma, ajout du PCB V1
    [bms.kicad_sch, motors.kicad_sch, power.kicad_sch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]
2026-04-01 Léger remapping du stm32.
    [stm32.kicad_sch, tank.kicad_pcb]
2026-04-03 Modifications mineurs du schéma. Passage sous Kicad 10 ok. Finalisations PCB (teardrops, arrondis)
    [tank.kicad_pcb, tank.kicad_sch]
